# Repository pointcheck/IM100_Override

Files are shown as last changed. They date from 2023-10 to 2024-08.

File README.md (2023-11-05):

# Paslode IM100C vendor lock-in override 

This repository contains PCB schematics and firmware for the device to override vendor lock-in for Paslode IM100C gas actuated nail hammer.

## Disclaimer

This small one weekend project is provided here solely for educational purpose to demostrate how weak and futile vendor lock-ins can be at places it should not be present in essence and how easy it is to overcome it. Note, that overcomming (removing) vendor lock-in is illigal in many countries even for personal use, one can be sued or fined for doing so. You've been warned!

## Details

Paslode IM100C is a gas actuated nailing system (stapling hammer) that uses natural gas (propane/butane mixture) to fuel hammer working by internal combustion principle, i.e. by injecting a dose of fuel into combustion chamber and igniting mixture with electrical spark, like it goes in any gasoline engine.

Paslode IM100C is very useful and handy device which can be used both by DIY and professional carpenters or wood workers. The problem is that fuel cartridges (cylindrical tanks with gas mixture) are equipped with RFID tags (NFC 13MHz standard) that store a decreasing counter of nails you can fire, usually not more than 1250 shots, thus limiting users and enforcing them to purchase "genuine" fuel cartridges. These cartridges come at a cost of course, somewhat about 100+ EURO each. Many users discovered that it is possible to refill cartridges with a gas purchased from nearby hardware store, but you still will be limited to a number of shots because of the above vendor lock-in mechanism.

One can disassemble IM100C hammer and see that vendor made significant effort to make lock-in hard to override. There are two MCU powered devices (PCBs) inside. One is controlling fuel injection and ignition mechanism, and the other for gas valve. It is the last one that prevents fuel to come from cartridge to the chamber if not proper (or outdated) RFID tag found. These two controllers communicate to each other using digital (I2C) interface. There are also two digital buttons that produce PWM signals on their outputs. One button is tied to shutter mechanism and signals when it is time to refill chamber with new dose of fuel, the other one is a fire trigger user pulls to make a nail shot. Both controllers (PCBs) are immersed into some kind of compound making reverse-engineering not easy to perform.

Yet, there is a way to work-around this vendor lock-in. A simple analysis shown that sparks are being produced even if hammer is missing proper fuel cartridge. So, if one can open gas valve in-time (and for a proper time period) to let fuel in into the chamber, the hammer will work. Thus, to overcome vendor lock-in a simple MCU device can be used to control gas valve directly bypassing vendor's mechanism. This MCU device should be connected directly to shutter button and to the valve, making valve to open for a 15ms when shutter button is pressed. It is not necessary to disconnect shutter button and valve from original electronics, one can keep them running in parallel.

It was discovered, that gas injection time varies depending on ambient temperature, i.e. injection time increases when temperature goes down. The maximum injection time is ~40ms at temperatures -20C. Thus an NTC thermistor was introduced into override PCB board schematics and simple aproximation table is used in software.

## Safty instructions

If you decide to implement this vendor lock-in override device, please make sure you disassemble and assemble back your hammer with a) bettery and fuel cartridge removed, b) with gas chamber emptied priorly. Not doing so may lead to unexpected gas ignition and shot causing serious injury! Also, test device with hammer fully assembled and all the nuts are tightened! Please, be precautious!

## Images

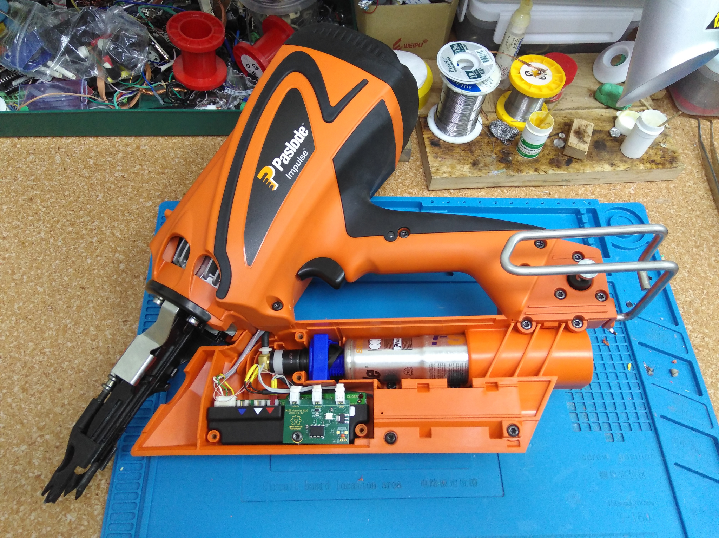
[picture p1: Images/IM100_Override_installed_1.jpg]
Paslode IM100C with vendor lock-in override installed


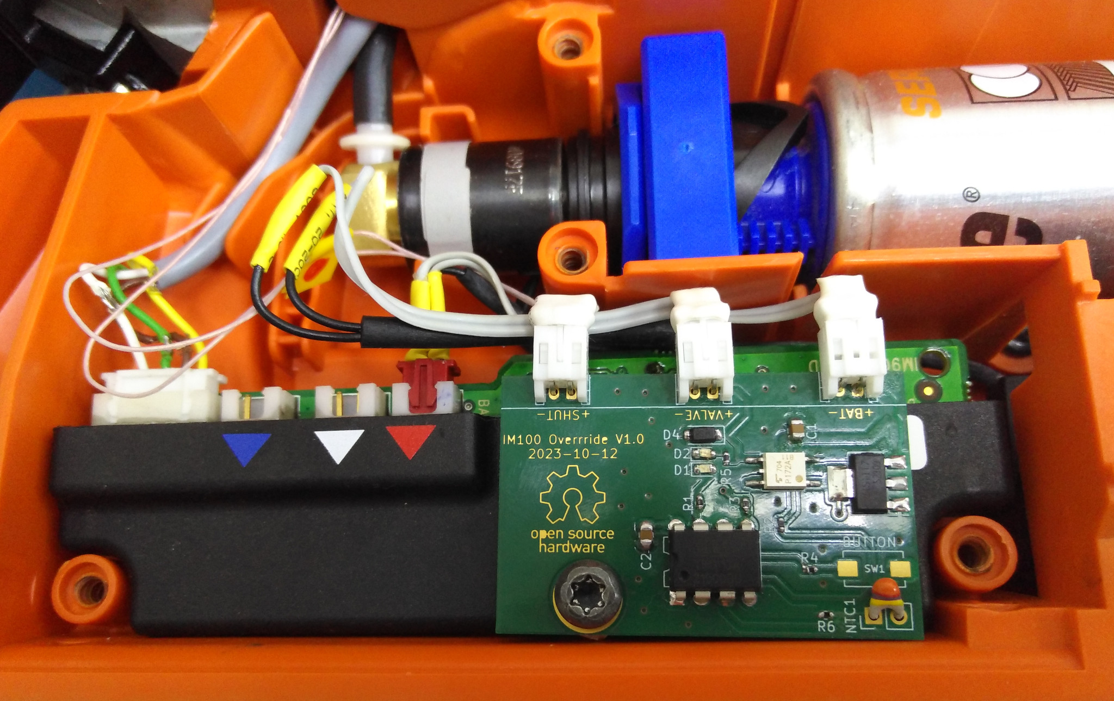
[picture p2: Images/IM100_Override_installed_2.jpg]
Paslode IM100C with vendor lock-in override installed


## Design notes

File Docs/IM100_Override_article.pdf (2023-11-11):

## Проект выходного дня: как снять электронный поводок с газового гвозде-забивного степлера Paslode Impulse

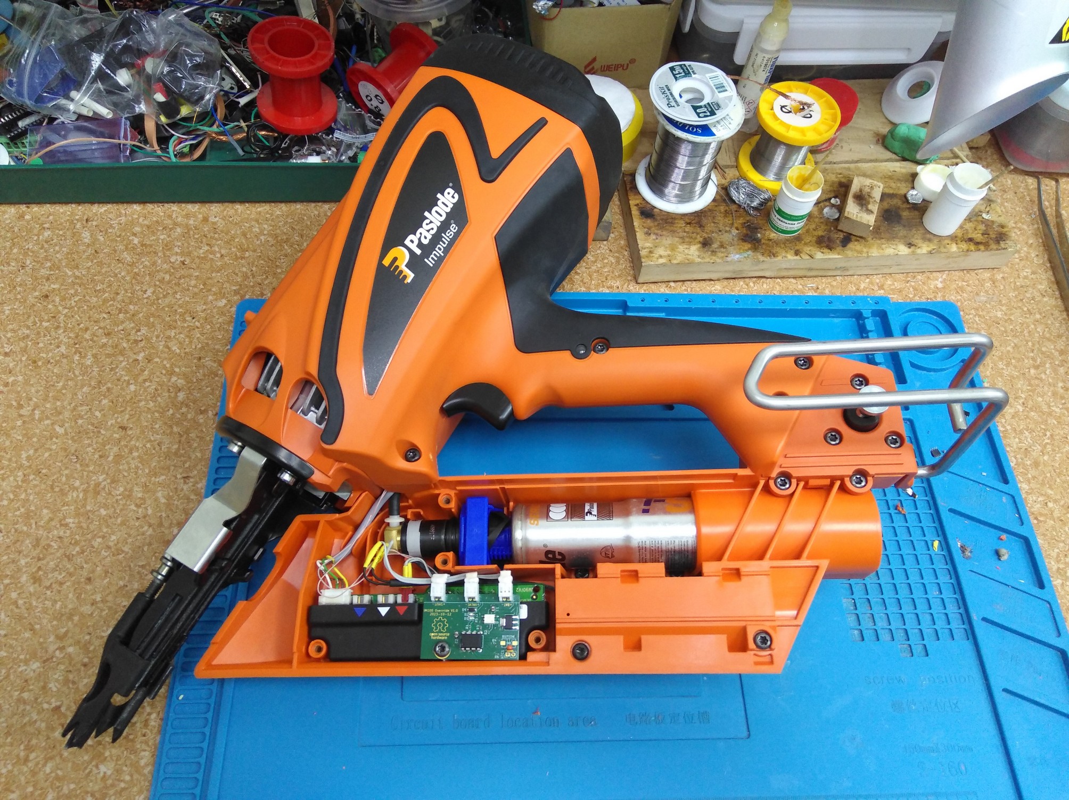
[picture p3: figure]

Рис. 1. Paslode Impulse IM100Ci с установленной платой блока обхода электронного поводка.

Пару недель назад ко мне обратился старый знакомый который занимается плотницким делом — строит дома, бытовые постройки, лестницы, мебель и прочую полезную дачную утварь из дерева. В этом деле ему помогает, правильней будет сказать «помогал» (и теперь надеюсь вновь будет помогать) замечательный инструмент — ручной гвозде-забивной газовый степлер Paslode Impulse IM100Ci про-ва Франция. Данный инструмент представляет собой ударный механизм оснащенный камерой сгорания, в которой происходит искровой поджег и детонация газовой смеси, продукты сгорания с силой выталкивают поршень ударяя бойком по гвоздю и оный со свистом заходит в доску. Всем процессом, разумеется, управляет электроника. Инструмент очень компактный, легкий, предназначен для работы на высоте и имеет адаптацию к температуре окружающей среды (может работать при -20С и ниже).
Но есть у данного инструмента одна неприятная особенность — баллончики с газом (обычный «природный газ» - пропан-бутановая смесь) оснащены RFID меткой стандарта NFC. В одной из ячеек памяти этой метки записывается счетчик «выстрелов». Всего производитель позволяет сделать не более 1250 выстрелов с одного баллончика. Баллончики с газом поставлялись только официальным дистрибьютером за совсем не малые 100+ EURO, а с введением санкций официальный канал поставки закрылся и ценник на них вырос в разы, что сделало данный инструмент практических не пригодным для применения. Разумеется такое положение дел очень сильно расстроило моего знакомого и он обратился ко мне с вопросом — а нельзя ли как-то того… отучить инструмент от этой совершено аморальной привязанности к производителю, ведь заполнить газом баллончик не представляет труда и обходится всего в 50 рублей! Посидев один свободный выходной день за приборами в нашей лаборатории мы пришли к выводу, что можно, и сделать это совсем не сложно.

## «Электронный молоток» изнутри

И так, вот, что мы увидели отвинтив десяток торксов и сняв крышку данного изделия. В изделии расположено две печатные платы с электронной начинкой — одна в «магазинной» части инструмента, другая в рукоятке. Обе платы погружены в «стакан» и залиты твердым компаундом — сразу видно, разработчики всячески старались усложнить работу всякому, кто попытается сунуться во внутрь их изделия (а как же «право на ремонт» мельком подумал я). По мимо двух плат в изделии были обнаружены: две цифровые (ШИМ) кнопки — одна срабатывает на положение затвора, вторая — на спусковой крючок (триггер); кастомный аккумулятор LiON на 7.2 номинальных вольта; электромагнитный клапан (соленоид); баллончик с газом, и RFID антенна кольцевой формы в центр которой входит верхняя (пластиковая) часть баллончика содержащая RFID метку. В отсеке с камерой сгорания располагается форсунка, а на задней крышке камеры расположен вентилятор для подвода газовой смеси и отвода продуктов сгорания и искровая свеча.
Питание от аккумулятора подводится к первой плате, расположенной в «магазинной» части инструмента, к ней же подключается соленоид клапана и RFID антенна. Две цифровые кнопки, вентилятор и свеча подключены ко второй плате (в рукоятке), а обе платы соединены между собой четырех-проводной линией связи.

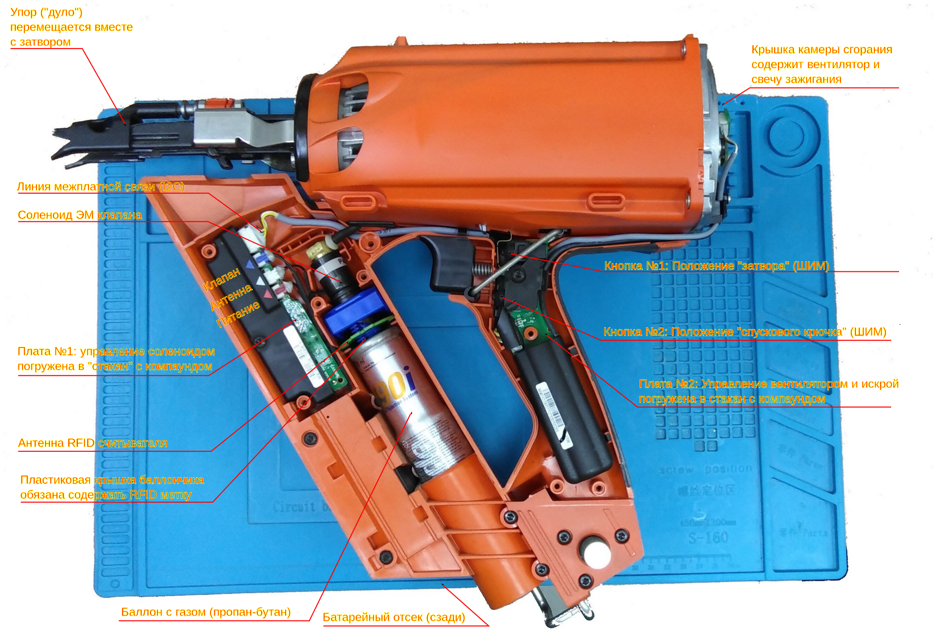
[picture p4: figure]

Рис. 2. Расположение элементов «электронного молотка» Paslode Impulse IM100Ci.

## Принцип действия «электронного молотка»

О общих чертах принцип действия данного гвозде-забивного инструмента можно описать следующим образом:
1. Инструмент подготавливается к работа: в него устанавливается баллон с газом, фрагмент ленты с гвоздями и заряженный аккумулятор который переводится в рабочее положение (вставлен до упора).
2. Оператор приставляет «дуло» инструмента к доске и прижимает его, тем самым происходит взвод затворного механизма, камера сгорания закрывается и срабатывается первая кнопка по сигналу которой происходит кратковременное открывание газового клапана (примерно на 14мс), газ поступает в камеру сгорания и одновременно с этим запускается вентилятор для смешивания газа с воздухом.
3. В следующий момент оператор нажимает на спусковой крючок (вторая кнопка), подается искра и происходит детонация, поршень с силой ударяет по бойку, который уперт в гвоздь и гвоздь заходит в доску.
4. После детонации камера открывается и из неё удаляются отработанные газы (продукты сгорания).

Для забивания следующего гвоздя оператор должен ослабить нажим на доску (на затвор), переместить «дуло» в другое место, прислонить к доске и нажать на спусковой крючок. По инструкции, инструмент может формировать до пяти «выстрелов» в секунду, но по факту получается не более двух, да и в этом случае надо быть весьма ловким парнем да-бы не всадить гвоздь куда не следует.

## Небольшое лирическое отступление

Я занимаюсь разработкой своей электроники и программного обеспечения к ней и, в общем, реверс-инжиниринг электронных схем и протоколов не входит в круг моих интересов и обязанностей. Ко мне не раз обращались с вопросами «как взломать лицензию» или «как обнулить счетчик» и таких вопрошателей я сразу отправляю в далекое путешествие с эротическим уклоном. Но в случае с этим «электронным молотком» меня что-то зацепило. С одной стороны хотелось как-то помочь старому товарищу в его беде — он так сильно был привязан к своему инструменту (и как профессионалу мне его очень легко понять), всячески нахваливал сам инструмент и производителя — не чета китайскому фуфлу, а тут этот производитель возьми и повернись к нему… задним лицом. И если уж не решить проблему, то хотя бы продемонстрировать невозможность решения в имеющихся у нас условиях. С дугой стороны, непрекращающиеся попытки производителей по всему миру привязать пользователя к своим расходникам или подпискам на бесполезные облачные сервисы, без которых изделие не может нормально эксплуатироваться, вызывает стойкое отвращение почти у каждого нормального человека. На сей счет в памяти всплыла статья с HN двухгодичной давности одного американского студента который отвязал посудомоечную машину от вендорных расходников и от вендорного «облака», тем самым существенно снизив расходы на её содержание, в результате фирма (стартап) тут же обанкротилась так как вся её ценность и безнес-модель строилась только на непрерывной «дойке» владельцев весьма посредственной бытовой машины. В общем, с «электронным молотком» у меня неожиданно возникло желание немного повозиться.

## Поиск решения

Идею реверсить саму RFID метку я оставил «на потом» - это весьма не простая задача для меня, требующая определенных навыков и оборудования, и что-то мне подсказывало, что на этом пути разработчики изделия подложили не мало ловушек. Вместо этого мы с товарищем решил поподробнее изучить электронную начинку изделия, и, прежде всего выяснить, почему в изделии две платы и какую функцию выполняет каждая их них. Эти платы имеют соединение между собой по четырем проводам. Путем незатейливого тыкания щупом мультиметра было обнаружено, что два из четырех проводов обеспечивают питание (+7.2В и «земля») второй платы от первой находящейся в «магазинном» отсеке, а два других — линия цифрового обмена. Анализ снятых осциллограмм показал, что по этим линия идет обмен в формате I2C, при этом плата в рукоятке является «слэйвом» и, как уже было сказано выше, именно к этой плате подключается RFID антенна и соленоид управления газовым клапаном.
Отключив антенну и попытавшись привести инструмент в исполнение, мы выяснили, что инструмент как бы пытается сработать, но что-то ему мешает: запускается вентилятор и даже выдается искра, всё как обычно, но детонации не происходит. Обмен по I2C тоже не меняется. Немного поразмыслив мы сделали предположение, что система не открывает (блокирует) клапан и в камеру не попадает порция газа. Косвенно это подтверждалось отсутствием специфического запаха газа, который присутствует при нормальной работе инструмента. Подцепив щуп осциллоскопа к проводникам идущим на клапан мы убедились в правильности нашего предположения. Тут же возникла идея подать газку «вручную», но для этого следовало понять какое напряжение подается на клапан и на какой интервал времени. Логика подсказывала, что слишком мало газа (обедненная смесь) или слишком много может привести либо к полному отсутствие детонации, либо к чему нибудь не очень хорошему — мы что нибудь повредим. Короче, мы подключили баллончик с RFID меткой и замерили осциллоскопом форму сигнала на клапане. Оказалось, что при комнатной температуре клапан открывается полным напряжением батареи на время 14 мс. Осталось придумать как подать такой импульс на клапан в обход первой платы.

Особенность данного изделия такова, что все натурные эксперименты (т. е. с реальной детонацией) следует проводить при полностью собранном инструменте и плотно закрытой крышкой, иначе есть шанс, что при детонации он разлетится на детали и может повредить кого-то или чего-то - инструмент весьма опасный. По этому было принято решение соорудить малогабаритный «наколеночный» прототип устройства платы обхода со своим микроконтроллером и встроить его внутрь инструмента, подключив все провода и полностью собрав инструмент. Данное устройство по сигналу (предположительно с кнопки затвора) будет формировать одиночные импульсы на клапан с некоторым интервалом и тем самым наполнять камеру сгорания газовой смесью.
В качестве миниатюрного и достаточно неприхотливого микроконтроллера был выбран МК ATtiny13A в корпусе DIP-8, а для подачи импульса на соленоид клапана было решено использовать имеющееся в наличии твердотельное реле TLP3123. Замер показал, что соленоид в открытом состоянии потребляет ток около 650 мА, что вполне вписывается в характеристики данного реле. В общем, плата устройства обхода была быстро собрана на текстолитовой макетке и тут же запрограммирована — благо ATtiny13A простой как валенок. Проблема возникла лишь в том откуда снимать сигнал управления, а следовательно требовалось понять в какой момент времени подается газ в камеру сгорания.
Как мы и предполагали, газ в камеру сгорания подается по кнопке механически соединенной с затвором, т. е. в момент когда оператор прислонил инструмент к доске и готов забить гвоздь. Однако, неожиданным оказалось то, что обе кнопки (затвора и спускового крючка) были цифровыми - формировали на выходе ШИМ сигнал пропорциональный степени нажатия. Мы попытались выяснить, влияет ли как-то степень нажатия этих кнопок на что либо (на силу удара, на частоту удара), но никакой корреляции обнаружено не было — в обычных условиях клапан инструмента всегда срабатывает когда скважность ШИМ достигает примерно половины, аналогично же подается искра. И, скажу честно, нам до сих пор не понятно зачем разработчикам данного инструмента потребовались столь навороченные кнопки с ШИМ выходом — уж не хотели ли они таким образом отпугнуть сторонних ремонтников. Короче, ШИМ с кнопки затвора был параллельно заведен на нашу плату обхода, а прошивка слегка доработана. Наше устройство мы назвали «Блок обхода электронного поводка - IM100 Override», прототип которого представлен на изображении ниже.

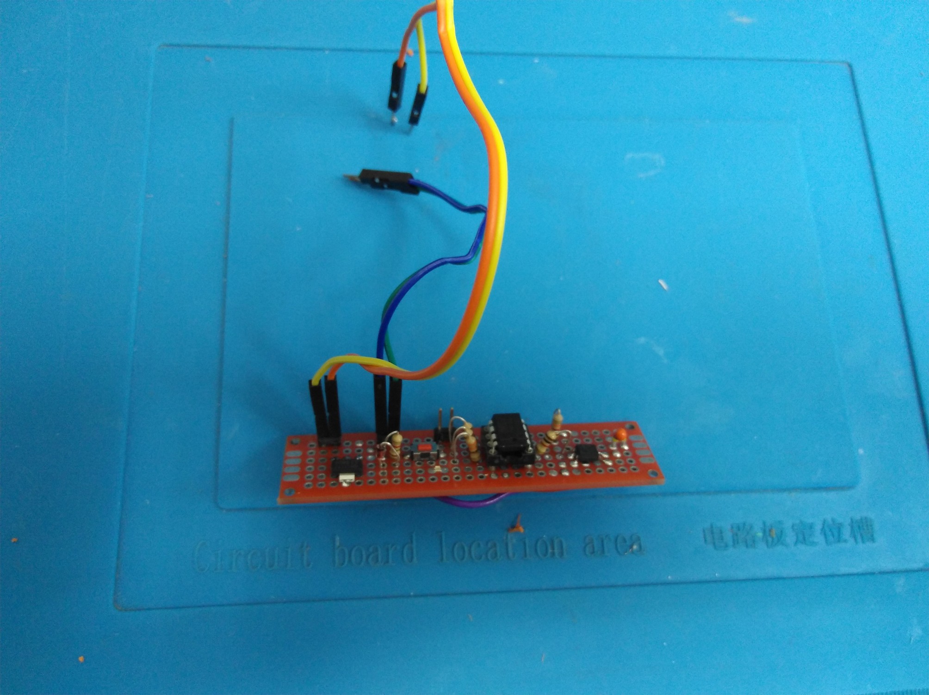
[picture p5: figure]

Рис. 3. Наколеночный вариант «Бока обхода электронного поводка IM100_Override»

## Первая проба «блока обхода»

Как это часто бывает, с первого раза у нас ничего не получилось. Мы протестировали блок обхода на разобранном изделии (без баллончика с газом) и убедились, что клапан открывается в нужный момент и на заданное количество времени, визуально инструмент работает «как настоящий». Но собрав всё воедино и закрыв крышки, забить гвоздь нам не удалось — детонация не происходила. Мы попробовали несколько раз, убедились в том, что газ поступает в камеру и формируется искра — но всё ни как. Меня начали посещать всякие странные мысли — а не повредили ли мы случайно какую либо из родных плат, или может быть всё гораздо сложнее и помимо подачи газа в камеру для работы инструмента требуется что-то еще. Я начал было подумывать, что пора уже свернуть «проект», и так весь день потрачен в пустую. Но тут случилось чудо — очередной раз приложив молоток к доске и нажав на курок мы услышало что-то похожее на… такое слабое «пук». Потом еще раз, и чуть громче, потом еще раз… и еще… но всё как-то тихо и без сильного удара по бойку. Т.е. детонация присутствовала, но была очень слабой. Мы бросили эксперименты и пошли пить кофе, а за одно принялись размышлять что же у нас такое происходит и почему в место громкого «бах» мы получаем редкое и тихое «пук».

## Вспоминаем как работает ДВС

В процессе обсуждения полученных результатов эксперимента в головы пришла простая аналогия — двигатель внутреннего сгорания. Всего-то нужно было вспомнить как работает ДВС, а именно — как и какая подается смесь в камеру сгорания и в какой момент происходит её поджег. Где-то из личного опыта, где-то из школьного курса физики вспомнилось, что: во-первых, что бы смесь воспламенялась она должна иметь определенные пропорции, если их нарушить то чуда не случится. Во-вторых, искра должна подаваться в нужный момент - с опережением. Допив кофе и вооружившись новым знанием (точнее, стряхнув пыль со старого), мы принялись крутить временные параметры подачи газа в камеру — это единственное на что мы могли в данном случае повлиять. И действительно, уменьшив интенсивность следования импульсов (вместо 200 мс мы установили интервалы 500 мс) и добавив небольшую задержку мы тут же получили искомый результат — четкая детонация и гвоздь в доске! Таким образом, отсутствие детонации в предыдущем эксперименте мы объяснили для себя слишком обогащенной смесью — так как импульсы поступают непрерывно, то камера успевает заполниться слишком большим количеством газа. Может быть это и не верное понимание физики процесса, но увеличение интервала между импульсами явно положительным образом сказывается на работе «электронного молотка».

## Адаптация под температуру окружающей среды

Как я уже упоминал выше, «электронный молоток» IM100c имеет встроенную автоматическую адаптацию к температуре окружающей среды и может работать при весьма низких температурах (до -30С). Наше предположение состояло в том, что контроллер управляющий инструментом регулирует количество подаваемого газа в камеру в зависимости от температуры. Опытным путем (заморозкой в климатической камере) было установлено, что при температуре окружающей среды -20С, длительность импульса составляет 28 мс, а при 0С — 18 мс соответственно.
В схему блока обхода был добавлен NTC термистор заведенный на пин одного из каналов АЦП микроконтроллера. Программное обеспечение было слегка расширено, добавлена «на глаз» рассчитанная табличка значений длительности импульса в зависимости от температуры. Всё это было собрано и успешно протестировано в уличных условиях при минус 5С. Тестированием при -20С еще ожидает своего часа.

## От прототипа к изделию

По результатам двухдневных изысканий я переработал устройство обхода — вместо макетки разработал схему и плату в САПР KiCAD по размерам подходящую для установки в один из отсеков «электронного молоток» как раз поверх оригинальной, без каких либо дополнительных крепежных элементов. Плата была заказана и изготовлена в Резоните, собрана и установлена в инструмент (см. фото). Весь этот проект «IM100 Override» выложен на GitHub и GitFlic в свободном доступе — возможно кому-то будет полезен.

https://github.com/pointcheck/IM100_Override.git

https://gitflic.ru/project/fabmicro/im100_override

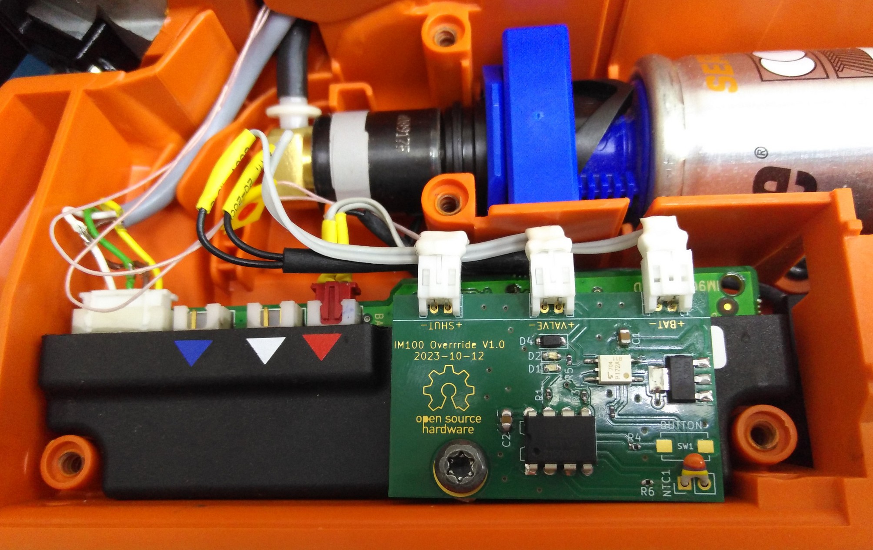
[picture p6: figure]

Рис 4. Плата обхода электронного поводка «IM100_Override» смонтированная в изделии.

Видео тестирования отремонтированного гвозде-забивного инструмента Paslode Impulse IM100Ci находится тут: https://www.youtube.com/watch?v=1oVWPjdFPZw

## В качестве заключения

Я хотел бы извиниться перед читателями которые ждали от статьи более обстоятельного исследования протоколов обмена, формата записи в хранилище на NFC метку и т. д. Всё это конечно можно было бы выполнить будь у меня немного больше свободного времени. Однако, как гласит народная мудрость — «настоящие герои всегда идут в обход», и в этом смысле предпринятое нами решение является демонстрацией того, что вся эта электронная привязка, особенно там где её быть не должно, не стоит вложенных в её разработку средств и легко обходится незатейливыми средствами. Более того, у меня даже возникла идея совсем избавиться от «родной» электронной начинки и сделать свою, добавил в блок обхода управление вентилятором и подачу искры, всего-то требуется хорошая емкость и умножитель напряжения.

С уважением,
Руслан.

e-mail: ruslan.zalata@gmail.com

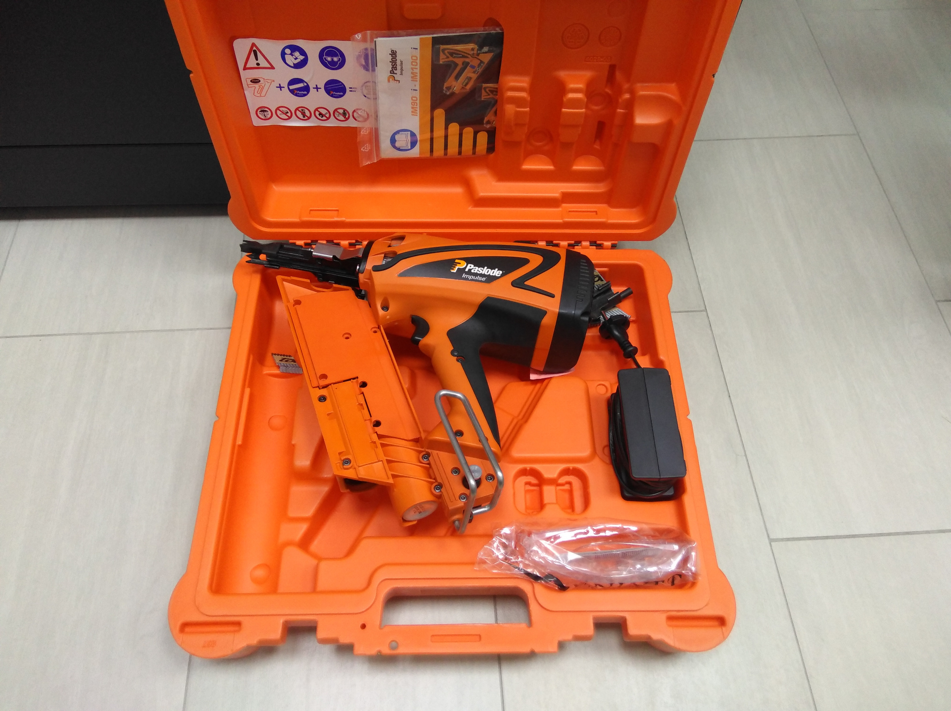
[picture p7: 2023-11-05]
Images/IM100_kit.jpg

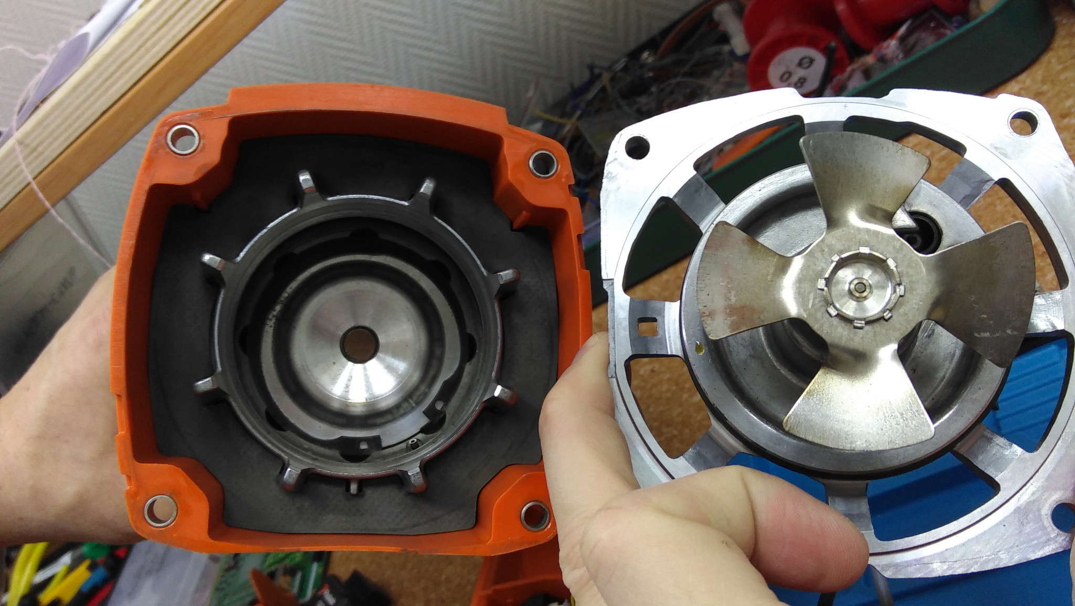
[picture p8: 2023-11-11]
Images/IM100_RearView.jpg

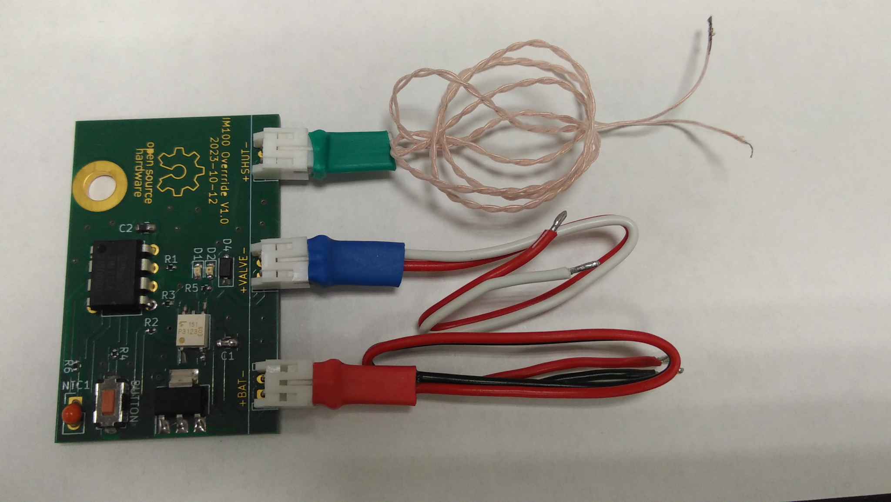
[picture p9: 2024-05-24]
Images/IM100_Override_kit.jpg

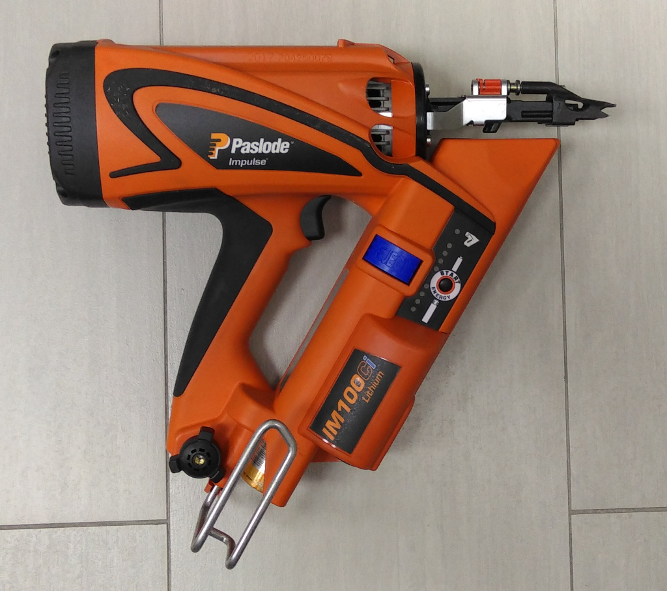
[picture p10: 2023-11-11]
Images/IM100Ci.jpg

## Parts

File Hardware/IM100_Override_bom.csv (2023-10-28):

Source: | /P/PROJECTS/IM100_Override/Hardware/IM100_Override.kicad_sch
Date: | Sat 28 Oct 16:27:46 2023
Tool: | Eeschema 7.0.2
Generator: | /usr/local/share/kicad/plugins/bom_csv_fabmicro.py
Component Count: | 20
Ref | Qnty | Value | Cmp name | Footprint | Description | Vendor | Mfr. Part Number
C1, C2, | 2 | 22uF/25V | CapacitorUnpolarized | Capacitor_SMD:C_0805_2012Metric |  |  | CL21A226MAQNNNE
D1, | 1 | FYLS-0603PGC | LED | LED_SMD:LED_0603_1608Metric | Light emitting diode |  | FYLS-0603PGC
D2, | 1 | FYLS-0603URC | LED | LED_SMD:LED_0603_1608Metric | Light emitting diode |  | FYLS-0603PGC
D4, | 1 | 1N4148W | 1N4148W | Diode_SMD:D_SOD-123 | 75V 0.15A Fast Switching Diode, SOD-123 |  | 1N4148W
H1, | 1 | MountingHole | MountingHole | MountingHole:MountingHole_4.3mm_M4_DIN965_Pad | Mounting Hole without connection
J1, J2, J3, | 3 | S2B-PH-K-S (LF)(SN) | CONN_2Pins | Connector_JST:JST_PH_S2B-PH-K_1x02_P2.00mm_Horizontal | Connector, 2 Pins |  | S2B-PH-K-S (LF)(SN)
NTC1, | 1 | 4.7K NTC | PT100 | Connector_PinHeader_2.54mm:PinHeader_1x02_P2.54mm_Vertical | PT100 platinum temperature sensor (RTD)
R1, | 1 | 330R/1% | Resistor | Resistor_SMD:R_0402_1005Metric |  |  | RC0402FR-07330RL
R2, R5, | 2 | 1K/1% | Resistor | Resistor_SMD:R_0402_1005Metric |  |  | RC0402FR-071KL
R3, R4, | 2 | 110R/1% | Resistor | Resistor_SMD:R_0402_1005Metric |  |  | RC0402FR-07110RL
R6, | 1 | 10K/1% | Resistor | Resistor_SMD:R_0402_1005Metric |  |  | RC0402FR-0710KL
SW1, | 1 | SW_Push | SW_Push | Button_Switch_SMD:SW_SPST_EVQPE1 | Push button switch, generic, two pins |  | DTSM-32
U1, | 1 | ATtiny13-20P | ATtiny13-20P | Package_DIP:DIP-8_W7.62mm | 20MHz, 1kB Flash, 64B SRAM, 64B EEPROM, debugWIRE, DIP-8
U2, | 1 | TLP3123 | TLP3123 | Package_SO:SO-4_4.4x3.9mm_P2.54mm | Solid State Relay (Photo MOSFET) 40V, 1A, 0.1Ohm, SO-4
U3, | 1 | AMS1117-3.3 | AMS1117-3.3 | Package_TO_SOT_SMD:SOT-223-3_TabPin2 | 1A Low Dropout regulator, positive, 3.3V fixed output, SOT-223

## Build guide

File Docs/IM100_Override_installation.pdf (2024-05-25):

## Инструкция по установке блока обхода ограничений «IM100_Override» для газового гвоздезабивного степлера «Paslode Impulse IM100Ci»


Рис. 1. Paslode Impulse IM100Ci с установленной платой блока обхода.

1. Назначение блока обхода «IM100_Override».

Блок обхода ограничений «IM100_Override» предназначен для снятия ограничений на количество забиваемых гвоздей с одного газового баллона у гвоздезабивного степлера Paslode Impulse IM100Ci. Принцип действия блока обхода сводится к тому, чтобы формировать сигнал управления соленоидом газового клапана в обход оригинальной схемы которая блокирует соленоид если в RFID метке расположенной в крышке баллона истек счетчик числа «выстрелов».

Блок обхода «IM100_Override» предназначена для самостоятельной установки. Для этого необходимо обладать базовыми навыками владения паяльником, бокорезами, отверткой и измерительным прибором (вольтметром).

Внимание! Установка блока обхода ограничений полностью лишит Вас гарантии на гвоздезабивной степлер, может повредить его без шанса на ремонт и овсстановление! Вы устанавливаете блок обхода на свой страх и риск!

2. Техника безопасности и меры предосторожности.

При установке платы блока IM100_Override необходимо помнить, что гвоздезабивной степлер является устройством повышенной опасности и при установки блока обхода необходимо следовать следующим правилам:

2.1. Разборку и сборку степлера, а также установку блока обхода проводите только с обесточенным и разряженным степлером.
2.2. Перед установкой, изымите из степлера обойму гвоздей, аккумуляторную батарей и газовый баллон и отложите их в сторону.
2.3. Будьте внимательны при разборке степлера, в его конструкции находятся мелкие детали и пружины которые могут легко выскочить и затеряться. Дальнейшая эксплуатация степлера без этих деталей будет невозможна.
2.4. При разборке степлера делайте фотографии расположения деталей. Это поможет правильно осуществить обратную сборку степлера.
2.5. Испытания работы степлера проводите только после его полной сборки — убедитесь, что все винты плотно затянуты, а детали находятся на своих местах. Испытания плохо собранного степлера может привести как к повреждению самого степлера, так и к причинить вред Вашему здоровью!
2.6. Соблюдайте полярность при подключении проводом блока обхода. Проводник с положительным напряжением всегда красного цвета. Обратите внимание на обозначения (+) и (-) расположенные на плате блока обхода возле разъемов.

Будьте бдительны, осторожны и аккуратны и у Вас все получится! :-)

### 3. Установка платы блока обхода

3.1. Плата блока обхода устанавливается во фронтальный отсек поверх оригинальной платы управления и фиксируется тем же винтом, что и оригинальная плата.
3.2. Полностью отсоедините аккумуляторную батарею, изымите газовый баллон и остаток гвоздей.
3.3. Развинтите и снимите крышку переднего отсека. Вам откроется вид на блок управления расположенный в черном пластиковом корпусе залитый компаундом. На блоке должны быть три разъёма:
«красный» - разъем питания +7В от АКБ.
«белый» - разъем подключения антенны считывателя RFID меток.
«синий» - разъем управления соленоидом газового клапана.
3.4. Отсоедините все три провод от этих разъемов. Снимите антенну RFID считывателя и уберите её, скорее всего она Вам больше не понадобится.
3.5. Подключите два провода блока обхода в параллель с существующими проводниками: «карсный» провод питания к «красному» проводу от АКБ, «синий» провод управления соленоидом к «синему» провод ведущему к соленоиду. Для осуществления подключения Вам придется оголить оригинальные проводники от изоляции, аккуратно подпаять проводники блока обхода и заизолировать места пайки. Как вариант, можно разобрать оригинальные разъемы и подпаять проводники блока обхода к контактам разъема в месте пайки оригинальных проводов, после чего собрать их обратно. При соединении необходимо соблюсти полярность, для этого можно воспользоваться измерительным прибором.
3.6. Отвинтите винт удерживающий оригинальный блок управления.
3.7. Не вынимая оригинальный блок управления, положите на него сверху плату блока обхода и закрутите фиксирующий винт обратно. При этом, под плату блока обхода можно подложить стальную шайбу соответствующего размера для того, чтобы плата блока обхода ровно легла на блок управления. Не затягивайте винт сильно, это может повредить печатную плату блока обхода.
3.8. Подключите три провода блока обхода («красный», «синий» и «зеленый») установив разъемы в соответствующие места на плате, как показано на рис. 2.
3.9. Подключите оригинальные провода к блоку управления в свои места, за исключением антенны RFID считывателя. Финальное расположение плат и подключенных к ним проводов показано на рис. 3.
3.10. Примерьте крышку переднего отсека, скорее всего Вам придется подрезать пластик в месте датчика температуры (компонент оранжевого цвета обозначенный на плате как NTC1). Удалите пластик с крышки острым ножом или горячим жалом паяльника. Убедитесь, что крышка плотно закрывается.

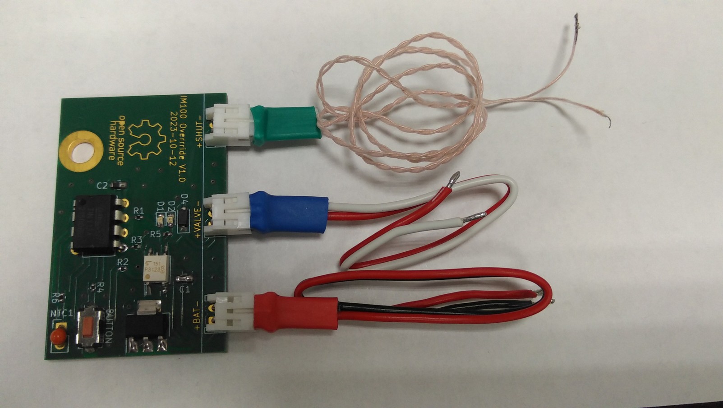
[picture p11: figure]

Рис 2. Плата блока обхода «IM100_Override» и цветовая маркировка проводов.

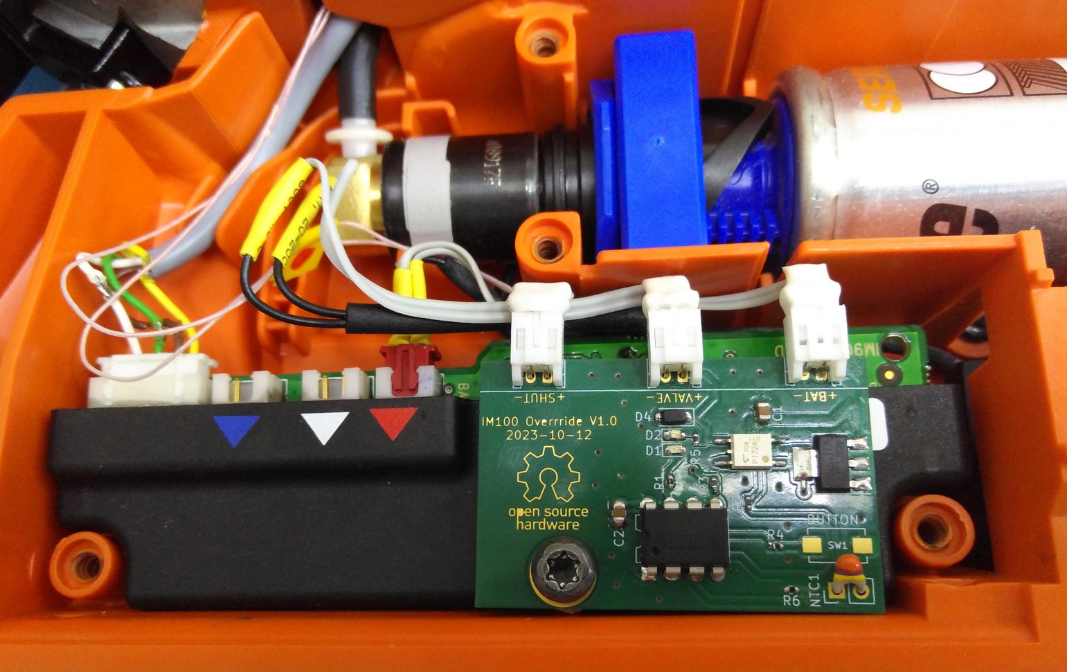
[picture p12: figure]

Рис 3. Плата блока обхода «IM100_Override» смонтированная в степлере.

### 4. Подключение к кнопке положения затвора

Третий «зеленый» провод блока обхода выполнен из тонкого провода типа МГТФ, его необходимо подключить к двум контактам кнопки положения затвора (Кнопка 1 на рис 4). Для этого следуйте следующим инструкциям:

4.1. Отвинтите винты удерживающие боковую крышку рукоятки степлера и снимите её.
4.2. Аккуратно приподнимите и переверните второй блок управления, содержащийся в рукоятке. Будьте внимательны к мелким деталям и положению пружины.
4.3. Найдите четыре контакта Кнопки 1.
4.4. Из четырех контактов первым необходимо подключить «общий». Обнаружить его не сложно с помощью прибора или просто внимательно присмотревшись - «общий» контакт имеет плотную связь с слоем металлизации на плате к которой припаян. Это контакт необходимо соединить с проводником «зеленого» провода выполненного из МГТФ и ведущего к контакту (-) на плате обхода.
4.5. По диагонали от «общего» контакта, на Кнопке 1 будет сигнальный контакт. Убедиться в том, что то именно он можно измерительным прибором — в пассивном состоянии и подключенной АКБ на этом контакте должно присутствовать напряжение +3.3В, а при нажатии кнопки напряжение будет падать до 1.5В или ниже. Все измерения проводите при отключенном баллоне!!!
4.6. Подключите сигнальный контакт Кнопки 1 к второму проводнику «красного» провода обозначенного на плате обхода как (+).
4.7. Аккуратно уложите провода внутри корпуса степлера и полностью соберите его.
4.8. Проведите испытания на «холостую», без гвоздей, упирая затвор степлера в доску.

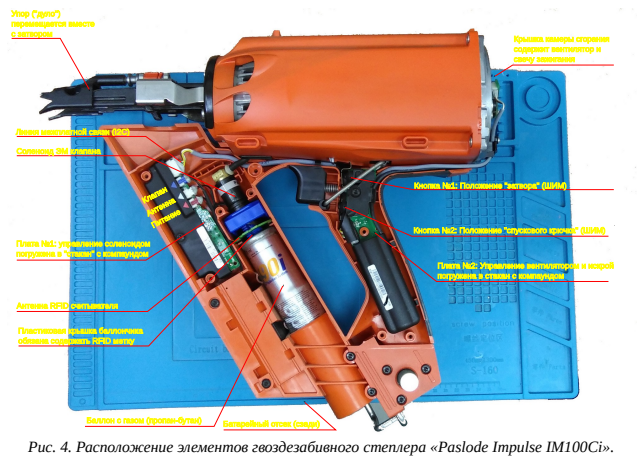
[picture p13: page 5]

Рис. 4. Расположение элементов гвоздезабивного степлера «Paslode Impulse IM100Ci».

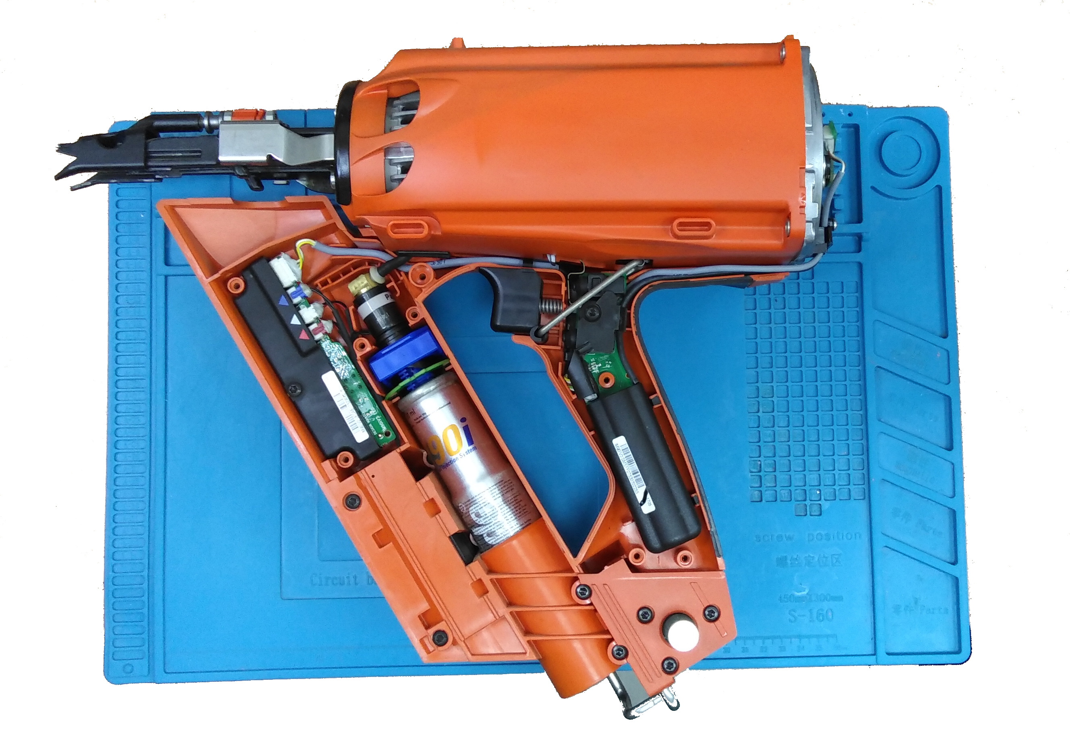
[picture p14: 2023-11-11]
Images/IM100_Disassembled.jpg

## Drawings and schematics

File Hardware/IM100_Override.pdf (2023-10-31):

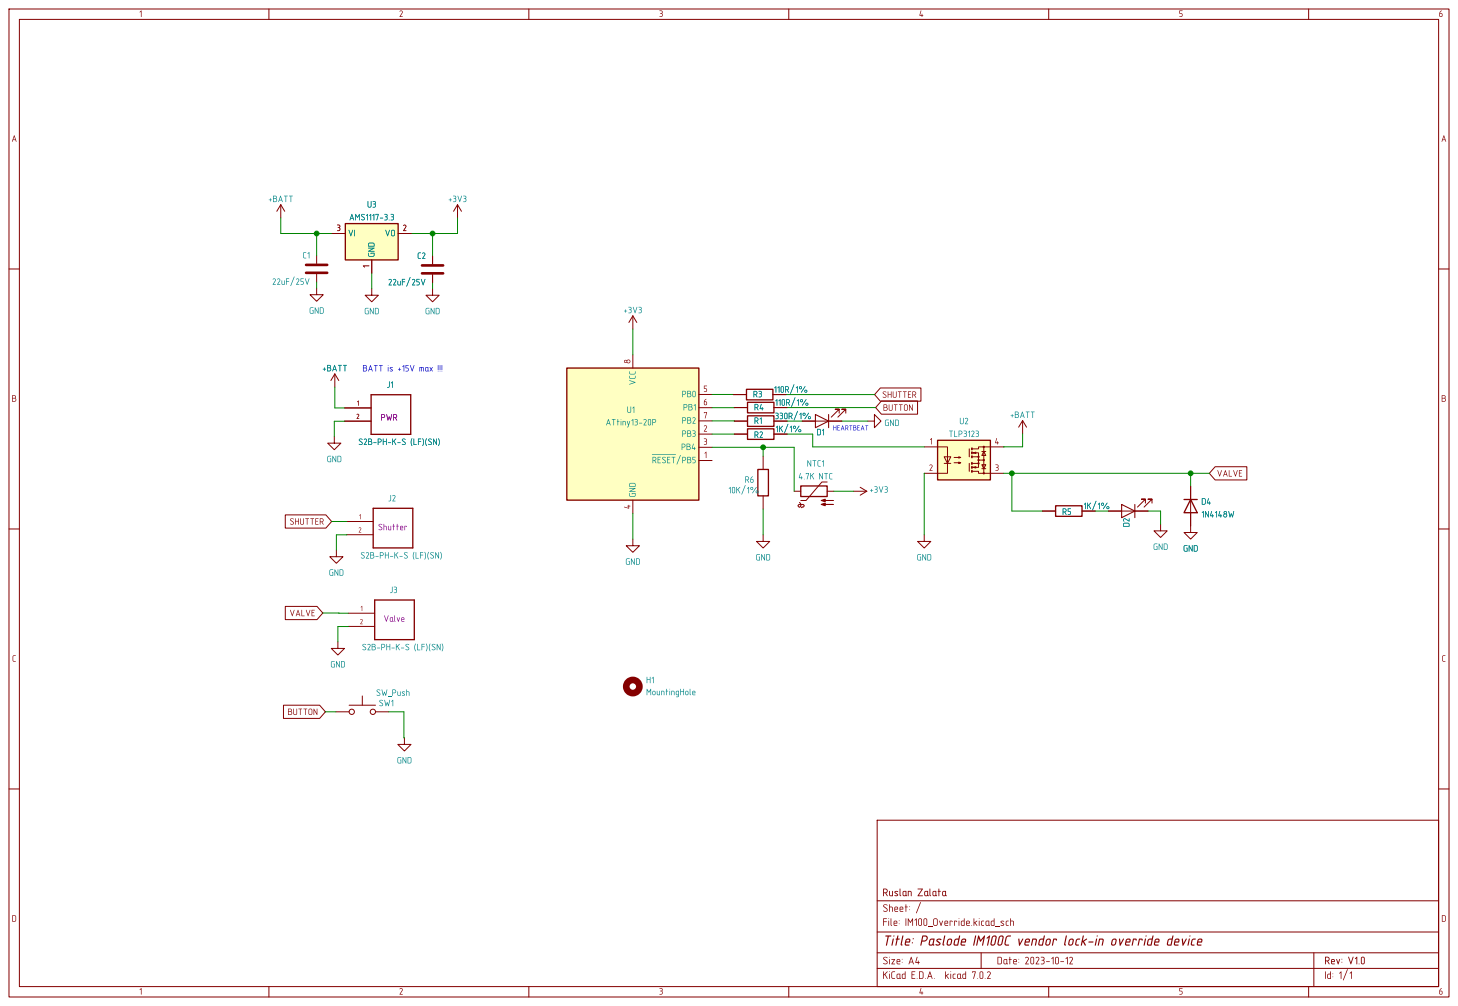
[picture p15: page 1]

J1 S2B-PH-K-S(LF)(SN) PWR

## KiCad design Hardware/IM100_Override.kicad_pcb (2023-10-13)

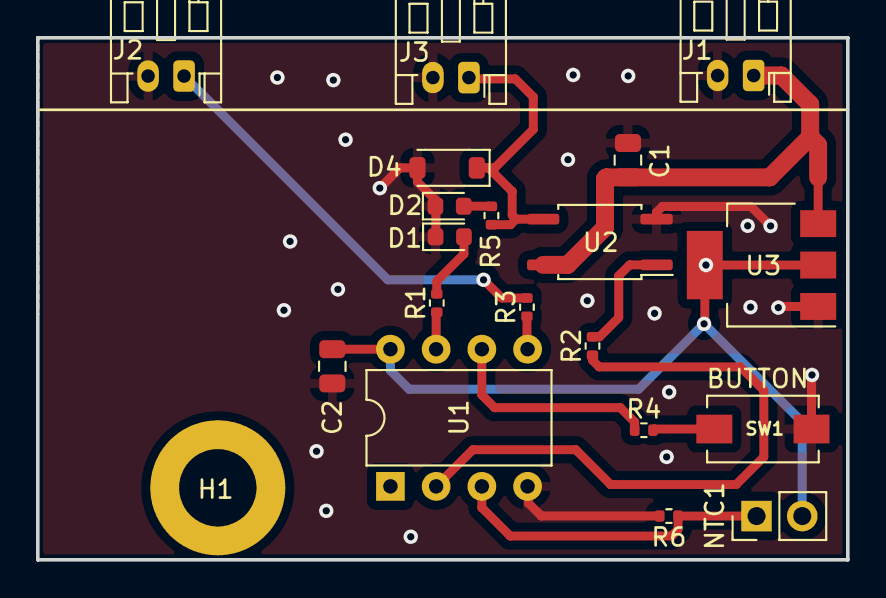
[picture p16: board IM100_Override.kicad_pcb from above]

Board: 2 copper layers, 45.0 x 29.0 mm, 20 parts (0 on the bottom side), 14 nets.

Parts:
C1, C2: 22uF/25V; C_0805_2012Metric
D1: FYLS-0603PGC; LED_0603_1608Metric
D2: FYLS-0603URC; LED_0603_1608Metric
D4: 1N4148W; D_SOD-123
H1: MountingHole; MountingHole_4.3mm_M4_DIN965_Pad
J1, J2, J3: S2B-PH-K-S (LF)(SN); JST_PH_S2B-PH-K_1x02_P2.00mm_Horizontal
NTC1: 4.7K NTC; PinHeader_1x02_P2.54mm_Vertical
R1: 330R/1%; R_0402_1005Metric
R2, R5: 1K/1%; R_0402_1005Metric
R3, R4: 110R/1%; R_0402_1005Metric
R6: 10K/1%; R_0402_1005Metric
SW1: SW_Push; SW_SPST_EVQPE1
U1: ATtiny13-20P; DIP-8_W7.62mm
U2: TLP3123; SO-4_4.4x3.9mm_P2.54mm
U3: AMS1117-3.3; SOT-223-3_TabPin2

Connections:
+3V3: C2.1, NTC1.2, U1.8 (VCC), U3.2 (VO)
+BATT: C1.1, J1.1, U2.4, U3.3 (VI)
BUTTON: R4.2, SW1.1
GND: C1.2, C2.2, D1.1 (K), D2.1 (K), D4.2 (A), J1.2, J2.2, J3.2, R6.2, SW1.2, U1.4 (GND), U2.2, U3.1 (GND)
unnamed: D1.2 (A), R1.2
unnamed: D2.2 (A), R5.2
unnamed: R2.2, U2.1
unnamed: R3.1, U1.5 (PB0)
unnamed: R4.1, U1.6 (PB1)
unnamed: R1.1, U1.7 (PB2)
unnamed: R2.1, U1.2 (PB3)
unnamed: NTC1.1, R6.1, U1.3 (PB4)
SHUTTER: J2.1, R3.2
VALVE: D4.1 (K), J3.1, R5.1, U2.3

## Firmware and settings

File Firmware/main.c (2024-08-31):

/*
 * Firmware for ATTINY13A MCU to control gas valve
 * in Paslode IM100C vendor lock-in override device.
 *
 * Copyright (c) 2023 Ruslan Zalata.
 *
 */

#include <stdlib.h>
#include <util/delay.h>
#include <avr/io.h>
#include <avr/interrupt.h>
#include <avr/wdt.h>

#define GAS_OFF_TIME_MS	500U
#define	VREF		3300UL	// Vref = Vcc = 3.3V

unsigned long sensor_mv = 0;
unsigned int pulse_ms = 14;

// ADC at -30C = 195mV
// ADC at -20C = 593mV 
// ADC at -10C = 920mV
// ADC at   0C = 2153mV
// ADC at +20C = 2244mV
// ADC at +30C = 2398mv

struct _temp_to_pulse {
	unsigned long adc_mv;
	unsigned int pulse_ms;
} temp_to_pulse[] = {
	{0, 42}, // at -60C
	{195, 42}, // at -30C
	{593, 36}, // at -20C
	{920, 20}, // at -10C
	{2153, 18}, // at 0C
	{2244, 14}, // at +20C
	{2398, 10}, // at +30C
	{3300, 10}, // sentinel
};

unsigned int calc_pulse(unsigned long adc_mv) {
	int i;
	unsigned int cur_pulse_ms = 0;

	if(adc_mv < 5)
		return 0; // Something is wrong with NTC sensor

	for(i = 0; i < sizeof(temp_to_pulse) / sizeof(temp_to_pulse[0]); i++)
		if(adc_mv >= temp_to_pulse[i].adc_mv)
			cur_pulse_ms = temp_to_pulse[i].pulse_ms;

	return cur_pulse_ms;
}

int main(void)
{
	cli();

	DDRB |= (1<<DDB2); // Output: Heartbeat LED
	PORTB &= ~(1<<PB2); // Turn OFF LED

	DDRB |= (1<<DDB3); // Output: Gas valve
	PORTB &= ~(1<<PB3); // Close Gass valve (active high)

	DDRB &= ~(1<<DDB0); // Input: Shutter trigger 
	PORTB |= (1<<PB0); // Enable pull-up for Shutter trigger

	DDRB &= ~(1<<DDB1); // Input: User button 
	PORTB |= (1<<PB1); // Enable pull-up for User button

	// PB4 (ADC2) pin is input
	DDRB &= ~(1<<DDB4); // Input: ADC2 
	PORTB &= ~(1<<PB4); // No pull-up for ADC2 
	// Set the ADC mux to ADC2, enable left adjust, Vref = Vcc
	ADMUX = (1 << MUX1) | (1 << ADLAR);
	// Set the prescaler to clock/128, enable ADC, no IRQ
	ADCSRA = (1 << ADPS1) | (1 << ADPS0) | (1 << ADEN);

	PCMSK = _BV (PCINT0); // Enable external interrupts PCINT0
	MCUCR = _BV (ISC01); // The falling edge of PCINT0 generates IRQ 
	GIMSK = _BV (PCIE); // Pin Change Interrupt Enable

	// Enable Watchdog
        WDTCR |= (1<<WDCE) | (1<<WDE); // Allow WDT reconfig, then enable WDT
	WDTCR |= (1<<WDCE) | (1<<WDP3); // Allow WDT reconfig, then set timeout to 4s
	wdt_reset();

	sei();

	// Long blink on statup
	PORTB |= (1<<PB2);
	_delay_ms(2000);
	PORTB &= ~(1<<PB2);
	wdt_reset();

	while (1) {
		// Start new the conversion
		ADCSRA |= (1 << ADSC);

		// Toggle Heartbeat LED once a second 
		PORTB ^= (1<<PB2);

		// Ping watchdog 
		wdt_reset();

		_delay_ms(1000);

		// Wait ADC to complete conversion
		while (ADCSRA & (1 << ADSC));

		// Read, cals and average temperature
		sensor_mv = VREF * (unsigned long)ADCH / 256;

		// Critical section
		cli();
		pulse_ms = calc_pulse(sensor_mv);
		sei();
	}

	return 0;
}

ISR (PCINT0_vect)
{
	cli();

	if ((PINB & (1<<PB0)) == 0) {
		int i;
	
		PORTB |= (1<<PB2); // Heartbeat goes LED ON when gas valve open
		PORTB |= (1<<PB3); // Open gas valve	

		// Keep pulse as long as pulse_ms miliseconds
		for(i = 0; i < pulse_ms; i++)
			_delay_ms(1);

		PORTB &= ~(1<<PB3); // Close gas valve	
		_delay_ms(GAS_OFF_TIME_MS);
		PORTB &= ~(1<<PB2); // Heartbeat is LED goes OFF 

		GIFR |= 0b01100000;
	}

	sei();
}


ISR (WDT_vect) {
}

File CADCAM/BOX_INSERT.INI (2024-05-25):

[Technics_Laser_Data]
ModifyTechCFG=0
LayersNumber=2
ExportRows=1
ExportColumns=1
ExportRowSpace=0.00000
ExportColumnSpace=0.00000
ExportRowCW=0.00000
ExportColumnCW=0.00000
LogicOrgPositionX=711.11593
LogicOrgPositionY=595.75741
LogicOrgPositionZ=-9999999.00000
AtOnceExport=1
IsTwoLaserWorking=1
TableZeroPositionX=0.00000
TableZeroPositionY=0.00000
OutputTimes=1
DelayTime=0
FeedLength=0.00000
FeedSpeed=5.00000
FeedDelayTime=0
MinX=451.29981
MaxX=711.11593
MinY=360.95470
MaxY=595.75741
ChangeSerialNo=0
ArrayMinX=451.29981
ArrayMaxX=711.11593
ArrayMinY=360.95470
ArrayMaxY=595.75741
LayerColor_0=65280
LayerColor_1=255
ClipBoxPower=40.00000
ClipBoxPower2=40.00000
ClipBoxOffsetLen=2.00000
ClipBoxSpeed=25.00000
AlignMachineZPos=0.00000
RouteLength=0.00000
RoutePointNumber=0
OffsetLaserPower=0.00000
OffsetWorkSpeedPer=1.00000
ZHeightForLaserFocus=0.00000
OneWorkNeedTimes=2
TotalWorkTimes=0
[CoordSystem_0]
LogicOrgPosition1=711.11593
LogicOrgPosition2=595.75741
LogicOrgPosition3=-9999999.00000
SPLITBLOCK_NUMBER=0
SPLITBLOCK_NUMBER_0=0.00000
SPLITBLOCK_NUMBER_1=100000.00000
[CreateTechnicsCodeMgr]
PrjHasModifyCFG=1
[TechnicsLayers_65280]
TechnicsMode=TECHNICS_LASERCUT
LaserCutConnerPower=10.00000
LaserCutWorkPower=20.00000
LaserCutConnerPower2=30.00000
LaserCutWorkPower2=50.00000
LaserCutFrequency=20000
LaserCutOptimizePathType=1
LaserCutInnerToOuter=1
LaserCutInnerToOuter2=0
LaserCutDownToUpper=0
LaserCutBlockHeight=150.00000
LaserCutAutoSetPathDir=1
LaserCutCicleMinSegNumber=36
LaserCutDisperseLength=0.10000
LaserCutCloseGapLength=0.00000
LaserCutOverlapLength=0.00000
LaserCutAdjustForClose=1
LaserCutQXEnterLength=0.00000
LaserCutDelayMoveTime=0.00000
LaserCutOpenGZDelayTime=0.00000
LaserCutOpenLaserDelayTime=0.00000
LaserCutCloseLaserDelayTime=0.00000
LaserCutDelayTimeAfterCloseLaser=0.00000
LaserCutOneAxisBackLashLength=0.00000
LaserCutTwoAxisBackLashLength=0.00000
LaserCutBackLashAddSpaceLength=8.00000
LaserCutBlowGasType=0
LaserCutAheadBlowGasTimes=0.00000
LaserCutNoCloseGasTimes=0.00000
LaserCutSpeed=100.00000
LaserCutGWAcc=3000.00000
LaserCutGWTime=0.01000
LaserCutTrackSize=100
LaserCutLineLength=0.00000
SpaceCutLineLength=0.00000
bSpaceLineFirst=0
LaserCutAdjustMove=0
LaserCutAdjustMoveDelay=0.00000
LaserCutUpLen=0.00000
LaserCutCircleSpeedNum=6
LaserCutCircleSpeed0_MinR=0.00000
LaserCutCircleSpeed0_MaxR=0.55000
LaserCutCircleSpeed0_Speed=10.00000
LaserCutCircleSpeed1_MinR=0.55000
LaserCutCircleSpeed1_MaxR=1.05000
LaserCutCircleSpeed1_Speed=15.00000
LaserCutCircleSpeed2_MinR=1.05000
LaserCutCircleSpeed2_MaxR=1.55000
LaserCutCircleSpeed2_Speed=25.00000
LaserCutCircleSpeed3_MinR=1.55000
LaserCutCircleSpeed3_MaxR=2.05000
LaserCutCircleSpeed3_Speed=30.00000
LaserCutCircleSpeed4_MinR=2.05000
LaserCutCircleSpeed4_MaxR=3.05000
LaserCutCircleSpeed4_Speed=35.00000
LaserCutCircleSpeed5_MinR=3.05000
LaserCutCircleSpeed5_MaxR=4.05000
LaserCutCircleSpeed5_Speed=40.00000
GROUP_ROWS_0=1
GROUP_COLUMNS_0=1
GROUP_ROWSPACE_0=0.00000
GROUP_COLUMNSPACE_0=0.00000
GROUP_ROWCWSPACE_0=0.00000
GROUP_COLUMNCWSPACE_0=0.00000
GROUP_MINX_0=482.62319
GROUP_MAXX_0=680.22001
GROUP_MINY_0=391.47239
GROUP_MAXY_0=564.33566
[TechnicsLayers_255]
TechnicsMode=TECHNICS_LASERCUT
LaserCutConnerPower=35.00000
LaserCutWorkPower=45.00000
LaserCutConnerPower2=30.00000
LaserCutWorkPower2=50.00000
LaserCutFrequency=20000
LaserCutOptimizePathType=1
LaserCutInnerToOuter=1
LaserCutInnerToOuter2=0
LaserCutDownToUpper=0
LaserCutBlockHeight=150.00000
LaserCutAutoSetPathDir=1
LaserCutCicleMinSegNumber=36
LaserCutDisperseLength=0.10000
LaserCutCloseGapLength=0.00000
LaserCutOverlapLength=0.00000
LaserCutAdjustForClose=1
LaserCutQXEnterLength=0.00000
LaserCutDelayMoveTime=0.00000
LaserCutOpenGZDelayTime=0.00000
LaserCutOpenLaserDelayTime=0.00000
LaserCutCloseLaserDelayTime=0.00000
LaserCutDelayTimeAfterCloseLaser=0.00000
LaserCutOneAxisBackLashLength=0.00000
LaserCutTwoAxisBackLashLength=0.00000
LaserCutBackLashAddSpaceLength=8.00000
LaserCutBlowGasType=0
LaserCutAheadBlowGasTimes=0.00000
LaserCutNoCloseGasTimes=0.00000
LaserCutSpeed=100.00000
LaserCutGWAcc=3000.00000
LaserCutGWTime=0.01000
LaserCutTrackSize=100
LaserCutLineLength=0.00000
SpaceCutLineLength=0.00000
bSpaceLineFirst=0
LaserCutAdjustMove=0
LaserCutAdjustMoveDelay=0.00000
LaserCutUpLen=0.00000
LaserCutCircleSpeedNum=6
LaserCutCircleSpeed0_MinR=0.00000
LaserCutCircleSpeed0_MaxR=0.55000
LaserCutCircleSpeed0_Speed=10.00000
LaserCutCircleSpeed1_MinR=0.55000
LaserCutCircleSpeed1_MaxR=1.05000
LaserCutCircleSpeed1_Speed=15.00000
LaserCutCircleSpeed2_MinR=1.05000
LaserCutCircleSpeed2_MaxR=1.55000
LaserCutCircleSpeed2_Speed=25.00000
LaserCutCircleSpeed3_MinR=1.55000
LaserCutCircleSpeed3_MaxR=2.05000
LaserCutCircleSpeed3_Speed=30.00000
LaserCutCircleSpeed4_MinR=2.05000
LaserCutCircleSpeed4_MaxR=3.05000
LaserCutCircleSpeed4_Speed=35.00000
LaserCutCircleSpeed5_MinR=3.05000
LaserCutCircleSpeed5_MaxR=4.05000
LaserCutCircleSpeed5_Speed=40.00000
GROUP_ROWS_0=1
GROUP_COLUMNS_0=1
GROUP_ROWSPACE_0=0.00000
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

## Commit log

2023-10-13 Initial commit: PCB schematics, board and gerber files
    [IM100_Override.kicad_pcb, IM100_Override.kicad_sch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]
2023-10-13 Add front/bottom mask to gerber files
    [IM100_Override-B_Cu.gbr, IM100_Override-B_Mask.gbr, IM100_Override-B_Silkscreen.gbr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]
2023-10-28 Add BoM file
    [IM100_Override_bom.csv]
2023-10-31 Output schematics file (PDF)
2023-11-01 Add temperature compensation through NTC sensor
2023-11-05 Add images with vendor lock-in override PCB installed on the device
2023-11-05 Update README: fix typos, add info about NTC sensor
2024-05-25 Add laser cutter CAM files for box insert
